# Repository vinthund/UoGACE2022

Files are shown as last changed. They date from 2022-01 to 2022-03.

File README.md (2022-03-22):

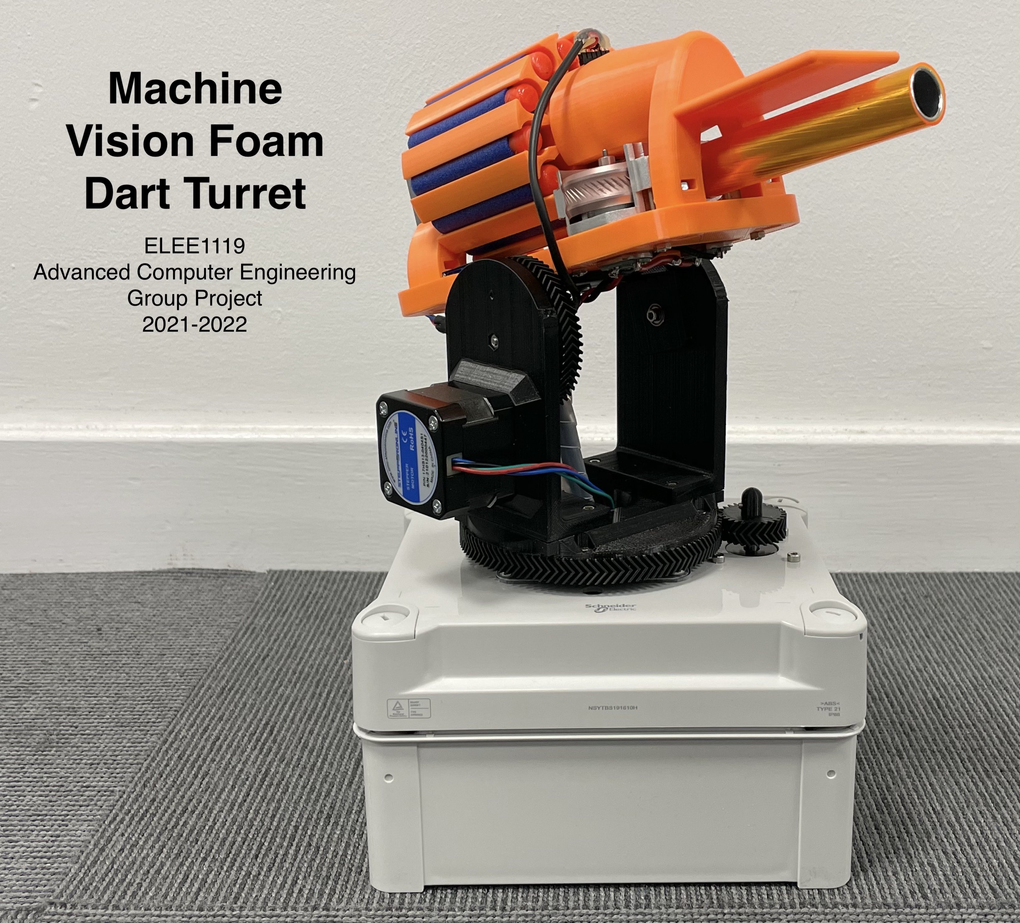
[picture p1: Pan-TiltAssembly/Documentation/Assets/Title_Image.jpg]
Title Image

<br>
## **About the Project**

This project has been developed by the contributors below as a submission of coursework for the University of Greenwich Advanced Computer Engineering Module, academic year 2021/22.

The Machine Vision Foam Dart Turret is a fully automated object targetting system designed to identify, target, and shoot (with a foam dart to two) a person not recognised by the machine vision. It features a 12 dart magazine, 2 axis movement, a Jetson Nano controlled vision system, and two interfaces (one for LAN based web control and video feedback, and one for automatic downloading of this GitHub repo).

Mechanical parts of this project are mostly custom using standard industry parts for difficult to manufacture parts such as stepper motors and bearings. The software is written mostly from scratch, using part libraries where sensible, particularily for the arduino interfacing with hardware, and the Jetson managing its machine vision identification.

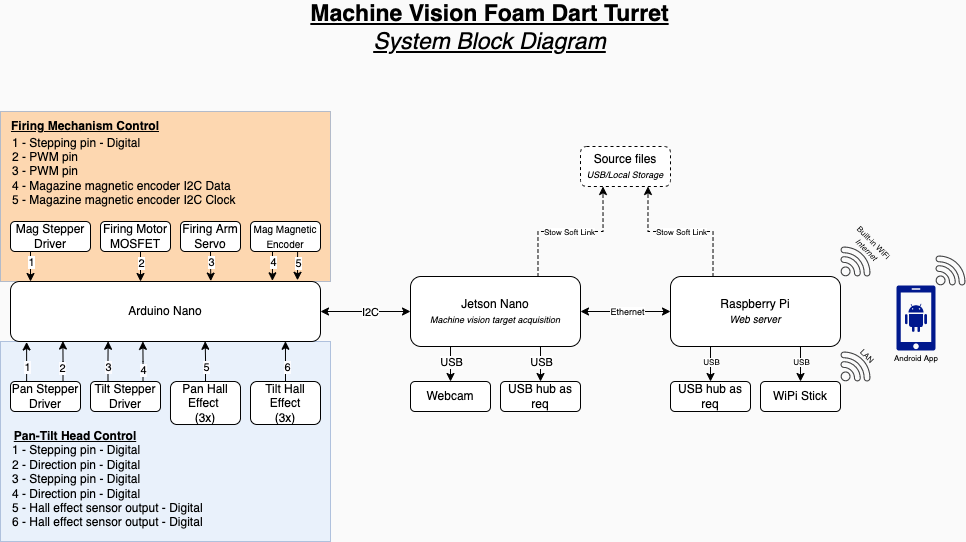
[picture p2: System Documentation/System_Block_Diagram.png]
System block diagram

*System Concept Block Diagram*

## **Contributors**

- [Andrew Dean - ad4646d](https://www.github.com/ad4646d)
- [Chris Halsall - ch6941r -](https://www.github.com/ch6941r)  [AfterEarthLtd](https://www.github.com/AfterEarthLTD)
- [vinthund](https://www.github.com/vinthund)
- [ht5640k - Harshitha Thimmegowda](https://www.github.com/ht5640k)
- [JoelSmalls - Joel A. Okanta](https://www.github.com/JoelSmalls)
- [kamyar123](https://www.github.com/kamyar123)
- [rowBoat](https://www.github.com/rowboat)
<br>

 ## **Viva Video**

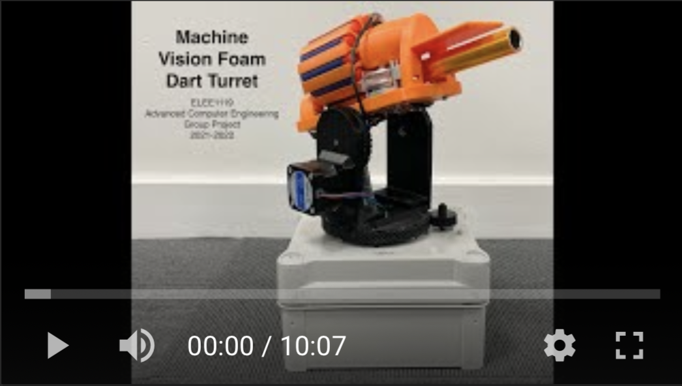
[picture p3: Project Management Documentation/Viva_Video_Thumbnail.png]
Viva_Video_Thumbnail (https://youtu.be/HJBah1AWvD8)


 ## **Firing Mechanism Mechanical Design** - [Chris Halsall - ch6941r](https://www.github.com/ch6941r)

The firing mechanism contains a few pre-made parts including a small stepper motor, the firing motors and barrel, a servo, and a bearing. All other parts have been designed in Fusion 360 and printed in orange PLA on an Ender 3 FDM 3D printer. It features a 12 dart rotary magazine driven by the stepper motor from one end and supported by a bearing at the other end. Through the bearing is mounted a magnet and a magnetic position sensor so that the control electronics can measure the angle of the magazine. A servo is mounted in the base and, with a custom arm, is capable of pushing a dart from the magazine into the firing motors and thus propelling it out of the barrel. A mounting plate is attached to the front of the design to securely mount the camera for machine vision. Finally, a hole and hex slot has been designed in to allow for easy mounting to the pan/tilt mehcanism.

The control electoronics includes an A4988 stepper driver, current limited to 0.5A per phase, an I2C connection for the magnetic position sensor, and a MOSFET (and protection circuitry) for driving the firing motors. These all interface with the joint Arduino Nano that controls all aspects of the moveable mech.
<br>
<br>

## **Pan-Tilt Mechanism Mechanical Design** - [Andrew Dean - ad4646d](https://www.github.com/ad4646d)

The [pan-tilt mechanism](https://github.com/vinthund/UoGACE2022/tree/main/Pan-TiltAssembly) is a bespoke 3D printed mechanism that was designed in tandem with bespoke the [firing mechanism](https://github.com/vinthund/UoGACE2022/tree/ad4646d/3D%20Designs/Firing%20Mech) using AutoDesk Fusion 360.

Herringbone gears were chosen for both pan and tilt axes for a number of reasons:
* They feature minimal backlash compared to 3D printed spur gears
* They are quieter in operation compared to 3D printed spur gears
* More torque can be transmitted through them vs 3D printed spur gears 

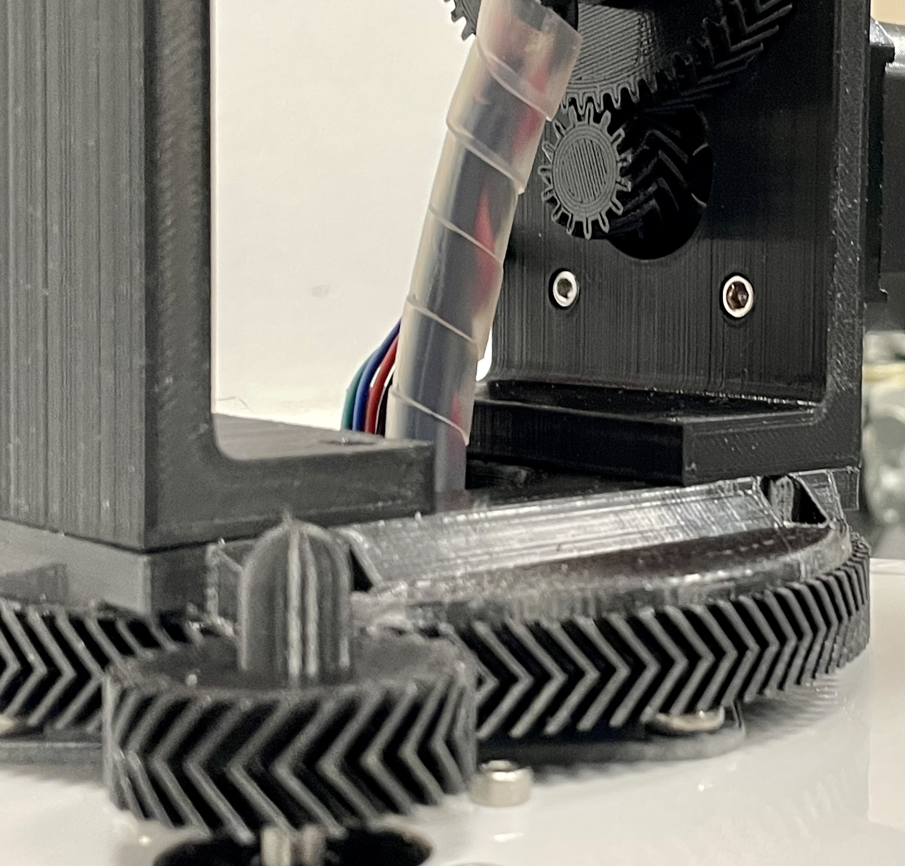
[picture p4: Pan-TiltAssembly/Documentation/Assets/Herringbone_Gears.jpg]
Herringbone_Gears


A plug-in for Fusion 360 called [GF Gear Generator](https://apps.autodesk.com/FUSION/en/Detail/Index?id=1236778940008086660&appLang=en&os=Win64) was used to generate the herringbone gears. \

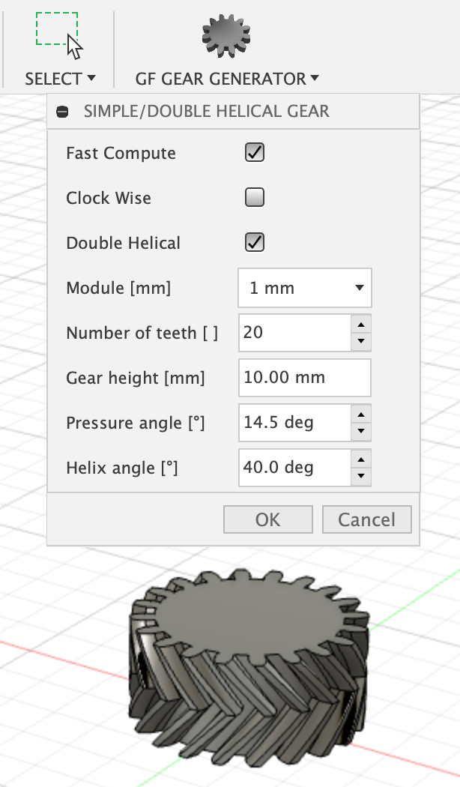
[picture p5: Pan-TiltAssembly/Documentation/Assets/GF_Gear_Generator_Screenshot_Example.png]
GF_Gear_Screenshot
 \
This produces a finished gear as a body, which can then be adapted 

The following parameters were found to produce gears with teeth that printed well and engaged with each other nicely.
> * Module - 1mm
> * Pressure angle - 14.5˚
> * Helix angle - 40˚ 

The number of teeth can be varied but the other parameters must remain the same for all meshing gears; the number of teeth and the module define the diameter of the gear:
> Diameter of gear = module x number of teeth

A gearing ratio of 4:1 was chosen to increase the torque output of the NEMA17 steppers and to give greater step-angle resolution.

The centre distance between the pinion gear and the output gear is calculated as follows:
> Centre distance = (Module*(No. teeth on pinion + No. teeth on output gear))/2

[Flange bearings](https://www.amazon.co.uk/gp/product/B07SHSLTKD/ref=ppx_yo_dt_b_asin_title_o03_s00?ie=UTF8&psc=1) are used to attach the tilt axis to the assembly, highlighted in the cross-section below.
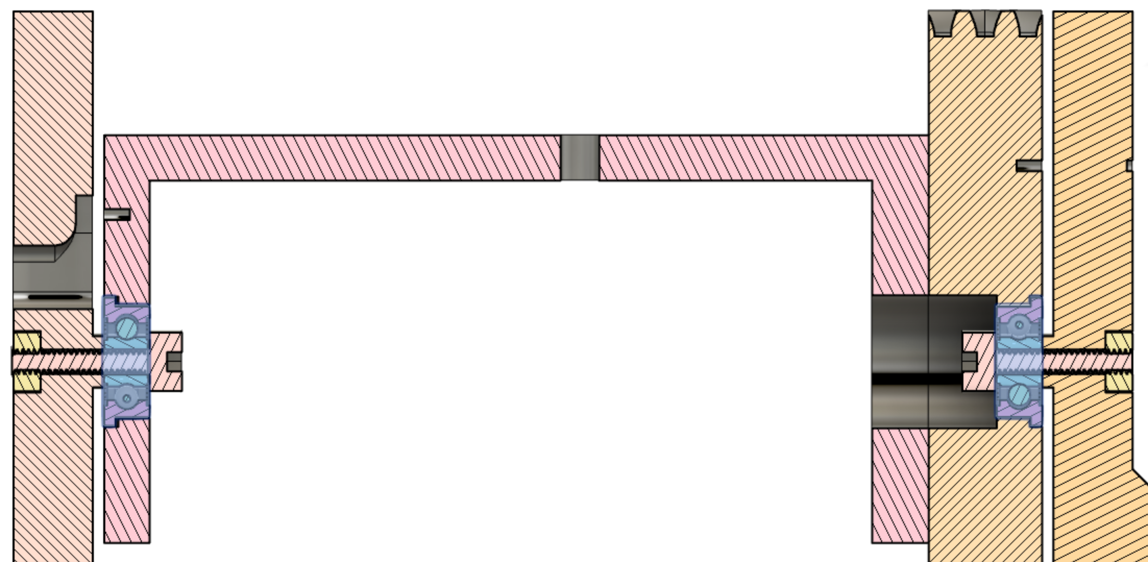
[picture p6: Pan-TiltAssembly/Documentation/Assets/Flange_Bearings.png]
Flange_Bearings
 
These flange bearings interference fit into the firing mech support bracket (pink) and tilt axis gear (yellow), removing the need for glue and simplifying assembly.

Locator pins have been designed into the bases of the two supporting supporting, these help to ensure that both supporting brackets are installed square to eachother, these are highlighted in the image below.
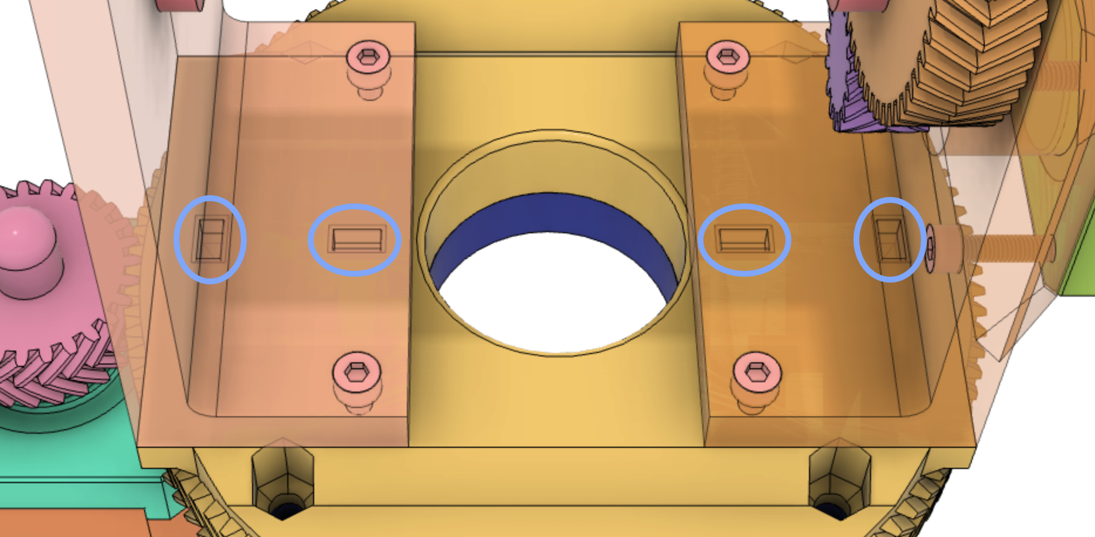
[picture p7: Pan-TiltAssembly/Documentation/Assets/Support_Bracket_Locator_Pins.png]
Locator_pins


All bespoke 3D printed parts for the pan-tilt mechanism were printed in black PLA using an Anycubic i3 Mega.

An [off-the-shelf electronics enclosure](https://www.screwfix.com/p/schneider-electric-ip66-weatherproof-outdoor-enclosure-164-x-105-x-192mm/) was chosen to be the base of the system, this particular enclosure was chosen as it would provide adequate space to house all system components.

A [lazy susan bearing](https://www.stilesandbates.co.uk/75mm-square-lazy-susan-bearing-1709.php) was chosen for the pan axis as it allowed for a convenient way to manage cables between the combined pan-tilt/firing mech and their control electronics in the enclosure below. \
The lazy susan did introduce a lot of audible noise to the system, this is due to a combination of the fact it is an unlubricated bearing and that the enclosure it is attached to was acting like a voice box, amplifying its vibrations. 
A foam pad was added between the bearing and the enclosure and the bearing lubricated with silicone grease, this helped somewhat with the audible noise. Half-step microstepping was also used to reduce the audible noise.

The full parts list for the pan-tilt mechanism can be found [here](https://github.com/vinthund/UoGACE2022/blob/ad4646d/Pan-TiltAssembly/Documentation/Pan-Tilt%20Head%20Parts%20List.pdf).\
STEP files for the pan-tilt mechanism can be found [here](https://github.com/vinthund/UoGACE2022/tree/main/Pan-TiltAssembly/CAD_Files).

<br>

## **Hardware for Pan/Tilt and Firing Mechanisms** - [Chris Halsall - ch6941r](https://www.github.com/ch6941r) & [Andrew Dean - ad4646d](https://www.github.com/ad4646d)
**Pan/Tilt Mechanism Hardware - [Andrew Dean - ad4646d](https://www.github.com/ad4646d)**

NEMA17 stepper motors were chosen for the Pan/Tilt axis as they provided adequate torque output to move both axes, they also feature a step angle of 1.8
* A [NEMA17x34](https://www.omc-stepperonline.com/nema-17-bipolar-1-8deg-26ncm-36-8oz-in-0-4a-12v-42x42x34mm-4-wires.html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) was chosen for the tilt axis
* A [NEMA17x39](https://www.omc-stepperonline.com/nema-17-bipolar-45ncm-6374ozin-15a-42x42x39mm-4-wires-w--1m-pin-connector.html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) was chosen for the pan axis

[A4988 stepper drivers](https://www.amazon.co.uk/gp/product/B07MXXL2KW) were selected for a number of reasons:
* They can drive bi-polar stepper motors up to 2A/phase
* They only require two control pins from the microcontroller to control steps and direction
* They can support microstepping
* They are still readily available amidst the current global component shortage

A combination of [small neodymium magnets](https://www.first4magnets.com/circular-disc-rod-c34/2mm-dia-x-2mm-thick-n42sh-neodymium-magnet-0-15kg-pull-p3327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|ps_1_16690) and [hall effect sensors](https://www.amazon.co.uk/gp/product/B08QCRYXPK) are used to both 'home' each axis and to and to limit the movement on the tilt axis, these were chosen over limit switches as they simplified mechanical assembly and design.

The hardware was connected up on a breadboard for testing ahead of the design of a veroboard prototype control board.

**Firing Mechanism Hardware - [Chris Halsall - ch6941r](https://www.github.com/ch6941r)**

## **Movement Control Circuitry** - [Chris Halsall - ch6941r](https://www.github.com/ch6941r)

A custom circuit board has been designed and built to accomodate the requirements for electrical control. A limitations prevented the use of a custom designed PCB including time, budget, and that continuous development was required therefore dynamically changing the structure of the circuit. A stripboard was chosen as it is relatively versatile and can accomodate throughhole components with ease. 

The bottom of the board is dedicated to power rails, 0V and 12V from an external PSU, and 5V generated by an L7805 linear regulator with the 12V input. All other board components are spread evenly to attempt to seperate wiring connectors as much as possible. The component parts are 
* Arduino Nano
* 3x A4988 stepper motor drivers
* 6x Hall effect sensor headers
* 1x Servo header
* 1x I2C header
* 1x MOSFET, flyback diode, and associated motor header

Some additional capacitors and a diode help to reduce input shock current (and therefore prevent brownout) and reverse power connection damage.

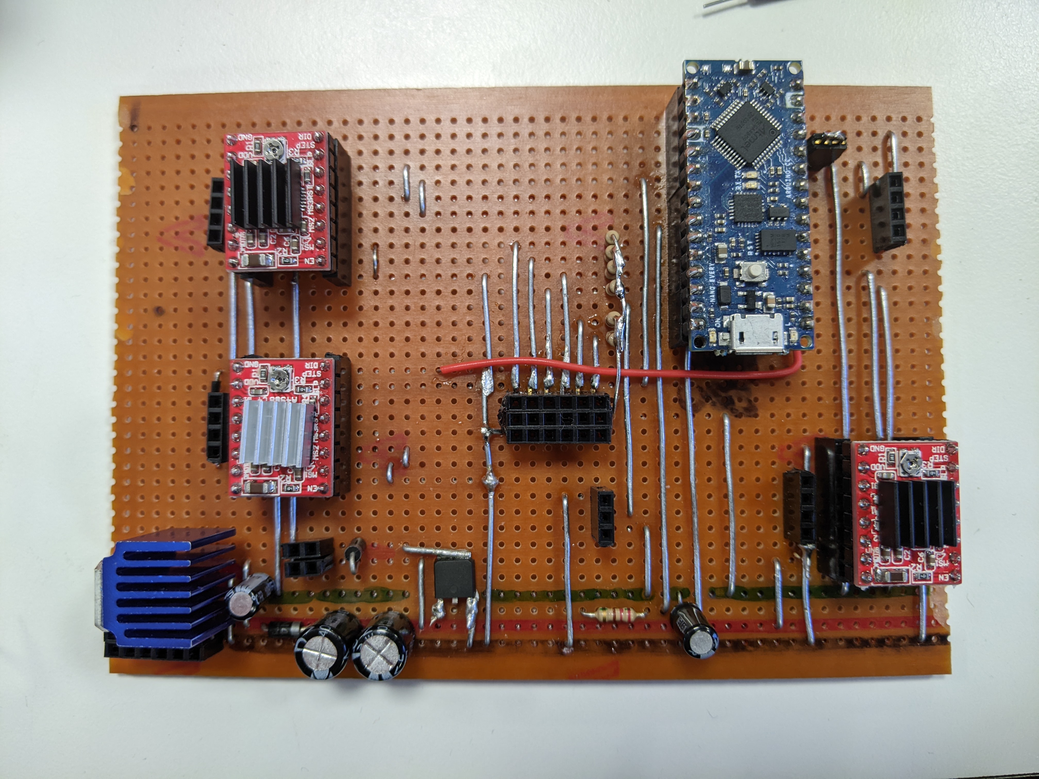
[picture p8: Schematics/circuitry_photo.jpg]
Control Circuitry


<br>

## **Firing Mechanism Communications** - [JoelSmalls - Joel A. Okanta](https://www.github.com/JoelSmalls)

**Items that were used**
* Raspberry Pi 3 Model B+
* Arduino Nano 
* Four Male to Female Jumper wires
* Four Male to Male Jumper wires
* Logic Level Shifter: Bi-Directional Module (Between 3V3 and 5V)
* Ethernet Cable: To allow for ssh into Pi to script in Python.

In order to make the control of the Firing Mechanism possible through communication between the Jetson Nano and the Arduino (shown on above diagram), a communications protocol had to be utilised. Types of communications protocols, such as I2C(Inter-Integrated Circuit), USB(Universal Serial Bus) Serial and SPI(Serial Peripheral Interface) were each investigated to see which would work efficiently when communicating between a Jetson Nano and an Arduino. As a Jetson Nano was not in possession, a Raspberry Pi was instead used to just simulate how certain communications protocols would work with each other.

The first iteration of a communications code between the Arduino and the Raspberry Pi was through USB Serial, in which a USB Cable was required to connect the Arduino straight to the Raspberry Pi. This was a simple type of communication which only required an Arduino USB Cable (dependent on board type) which could freely be moved around due to the length of the cable. However, we  had later anticipated that it would be necessary for a keyboard and mouse USB input to be left available on the Jetson Nano in case of errors. Thus, this idea was scrapped and was moved on to other types of communications protocols.

Other protocols such as I2C and SPI were explored. According to research, when comparing between I2C and SPI, SPI was a faster option; this did not mean it could be instantly utilised though, as not enough examples of communication between an Arduino and a Jetson/Pi could be found online to make use of SPI. Furthermore, it required more wires to be connected to the Nano through a logic level shifter. Due to this, I2C was settled with. 

This, was initially the case, on utilising I2C Communication to transmit data between the Raspberry Pi and the Arduino. Unfortunately though, as the gun firing mech used a sensor which required the Arduino to be a master over I2C, this idea of using I2C could not be applied. Providentially, there was another type of communications I had found through research, named Serial UART. Serial UART, according to research, is a "hardware communication protocol" that uses "asynchronous serial communication", meaning that unlike I2C, it does not have to synchronise to a clock signal. UART was made possible with a library named **SoftwareSerial** on the Arduino, and a library named **Serial** on Python were used to replace the original I2C system implemented.

**Setup**

[I2C]
The Arduino's SDA (Serial Data) was connected to the High Voltage(HV) pin 1, SCL (Serial Clock) at HV2, Arduino 5V at the HV input pin and Arduino Ground to the shifter's Ground. These were connected to the High Voltage due to the Arduino operating at an output of 5V.

The Raspberry Pi's SDA was connected on Low Voltage pin 1, opposite that of the Arduino's SDA connection; SCL was connected to LV2, 3V3 at LV input and Pi Ground to the shifter's ground. The Pi was connected to the Low Voltage side due to the Pi's output voltage being 3V3.

To fully use I2C, the Arduino and the Raspberry Pi's Python 3's libraries were used, being ***wire*** and ***smbus2*** libraries respectively.

[UART]
SoftwareSerial's library allows for the creation of Rx Tx pins over any digital pins, so 2 and 3 were selected in this case. Pin 2, Rx, was connected to HV1 of the logic level shifter; Pin 3 Tx was connected to HV2. Arduino 5V was connected to the HV of the Level Shifter, along with Arduino Ground connected to the component's ground. Similar steps were taken on the opposite side, with the Raspberry Pi's Tx on pin 8 connected on the opposite of the Arduino's Rx. Same followed for the Pi's pin 10 Rx connected opposite the Arduino's Tx on the shifter. The Pi's 3V3 Power was connected to LV, along with the Pi's ground connected to the component's ground.

I22ImagePiArduino

UARTExample

<br>

##  I2C Communicatons , Jetson Nano  - [ht5640k- Harshitha Thimmegowda ](https://www.github.com/ht5640k)

 **Jetson NANO** 

Items used

* Jetson nano
* HDMI cable

To get the Jetson Nano started:
* Basic files were installed.
* Stow was used which is a symlink farm manager which takes distinct sets of software and/or data located in separate directories on the filesystem, and makes them all appear to be installed in a single directory tree.
* Aliases were created to make abrieviation to soomthen the further procedures.
* Created /etc/network/interfaces  

**I2C communications**

Items used

* Raspberry Pi 3 Model B+
* Arduino Nano 
* Four Male to Female Jumper wires
* Four Male to Male Jumper wires
* Logic Level Shifter: Bi-Directional Module (Between 3V3 and 5V)
* Ethernet Cable: To allow for ssh into Pi to script in Python.

Above mentioned items were used to setup a to make an effictive communication to get the hardware working The Arduino's SDA (Serial Data) was connected to the High Voltage(HV) pin 1, SCL (Serial Clock) at HV2, Arduino 5V at the HV input pin and Arduino Ground to the shifter's Ground. These were connected to the High Voltage due to the Arduino operating at an output of 5V.
The Raspberry Pi's SDA was connected on Low Voltage pin 1, opposite that of the Arduino's SDA connection; SCL was connected to LV2, 3V3 at LV input and Pi Ground to the shifter's ground. The Pi was connected to the Low Voltage side due to the Pi's output voltage being 3V3 to get the RapberryPi and Arduino communicating.


**Shortening of ethernet cable**

Items used

* Ethernet cable
* Crimping tool
* Cable Connectors

Above mentioned items were used to shorten a ethernet cable to connect RaspberryPi and Jetson nano, It was done by cutting the available ethernet cable to the required length using a crimping tool and then pushing the wires into the cable connecter. Shortening was required in order to meet the hardware modeling requirement and to adjust the length of the ethernet cable connection very small and convenient.
Screenshot_20220318-221013_Snapchat

<br>

## **Machine Vision Target Aquisition** - [vinthund](https://www.github.com/vinthund)

Motion Detection in Python Version 1.0.0 
Written By Sian Pugh, sp3045k@gre.ac.uk, fleetfootgreyhound@gmail.com, vinthund @ github

Simple backend motion detector written in Python. Intended for use on a Jetson Nano 2gb to communicate with an Arduino system.

Part of a larger project used to control an autonomous nerf sentry - https://github.com/vinthund/UoGACE2022

Currently uses a subtractive method; it will take the first frame of input and store it as the "background", then compare all following frames to this. It has a threshold mechanism in place to ensure that small differences such as shadows are not seen as motion. When motion is detected using this subtractive method, a countour of the motion is drawn, as well as a retangle constructed of the area around it. This rectangle is used for specific targetting; the center is found and then compared to the center of the screen, with the results being sent to the arduino control unit using i2c.

Dependencies: This program requires the numpy and opencv packages to be installed to function. https://numpy.org/ https://opencv.org/

<br>

## **Web Server and Website** - [rowBoat](https://www.github.com/rowboat)

The website consist:
Was constructed using the php files in order to connection and retrieve data from the mysql server.
* The Login page - the first page that the user will see
* The Home page - once the user has logged in this is the next page that they will be greeted by. this page will consist of the window to the view the live video feed from the turret, a reading of how much bullets are left anda button for manual control. 
* A link to the github repository

Webserver
OS: Ubuntu
Wireless or wired: wireless
Configured in a lemp stack using nginx, mysql and php
Created to:
* Host the website
* Store login information
* Store and Retrieve video feed and bullet count from the camera and jetson so it could be displayed on the website and app
* Stores and sends button click to the jetson so when turret reacted to the corresponding button input.

<br>

## **Machine Vision Foam Dart Turret App** - [Kamyar Homampour-kamyar123](https://www.github.com/kamyar123)

This app has few pages which are:

* Login page

* Register page



* Main page

* Live page

Firebase has been used as a database for the login and register page to save all users' information and account date of the last login and created the account.


The main page was supposed to count the bullets, but due to circumstances, it hasn't been completed.

The live page was supposed to show the live stream from the jetson nano camera, but now it shows the test stream for rtsp link to test  if the live stream is actually working.
(https://www.wowza.com/developer/rtsp-stream-test)

<br>

## **Project Management** - [Andrew Dean - ad4646d](https://www.github.com/ad4646d) & [Chris Halsall - ch6941r](https://www.github.com/ch6941r)

When the project was announced, we asked all team members to detail their prior skills and experience on a [shared word document](https://github.com/vinthund/UoGACE2022/blob/main/Project%20Management%20Documentation/ELEE1119%20Team%20List%20(AD%20created).docx).

This initial skillset list was used to inform the project specification and division of tasks, which can be found in [this word document](https://github.com/vinthund/UoGACE2022/blob/main/Project%20Management%20Documentation/Project%20Specification%20and%20Division%20of%20Work%20(rev3).docx).

After everyone had agreed to the contents of the specification and the division of work, a [Gantt chart was created in MS Project](https://github.com/vinthund/UoGACE2022/blob/main/Project%20Management%20Documentation/ELEE1119_Project_Plan_7th_Dec_2021.mpp) to give an overview of the project timeline and to clearly communicate deadlines.

After the Gantt was shared with the team, a [KANBAN was maintained within GitHub](https://github.com/vinthund/UoGACE2022/projects/1). This KANBAN would get updated every Tuesday during the weekly standup meeting to establish what tasks people had in-progress and what tasks they had outstanding.

<br>

## **GitHub Management** - [vinthund](https://www.github.com/vinthund)

***Add your summary of work here and delete this comment.***

<br>

# **License**

Due to the sensitive nature of projectile firing technology, much thought has gone into the ethics of releasing a publically available repository with details of how the project was created. Please note that the content contained within this repository should be used solely for EDUCATION purposes. For full details please see the [License](LICENSE) document found in the root of this repository. This license has been based upon the MIT license.

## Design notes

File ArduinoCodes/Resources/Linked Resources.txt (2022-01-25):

AS5600 Magnetic Position Sensor Library
https://github.com/kanestoboi/AS5600

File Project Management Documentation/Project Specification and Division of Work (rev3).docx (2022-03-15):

# Project Specification and Division of Work

ELEE1119 Advance Computer Engineering

## Project Title

Automatic ‘Nerf’ Sentry Gun utilising Face or Object Recognition and Target Tracking

## Project Brief

To develop a prototype automatic foam dart blaster sentry gun capable of identifying targets, then actively targeting, and firing at them.

## Project Objectives

1. Design and create a custom firing mechanism capable of firing foam “Nerf” darts.
2. Design and create a dynamic mounting system capable of accurately controlling the firing direction.
3. Develop a bullet counting system with scope to incorporate reloading mechanics if the design permits.
4. Develop face or object recognition software capable of identifying predefined threats and feeding back data on their location for targeting.
5. Develop a remotely accessible monitoring and/or control system, e.g. mobile app or hosted website.
6. Develop an automatic log to capture all important activities, e.g. motion detection, user logon, firing at a target, etc.

## Project Methodology

From the ‘Team List’ document our individual skills have been identified.

Team Member’s Skills
Andrew Dean | Chris Halsall | Joshua McField | Kamyar Homampour | Joel Okanta | Sian Leigh Pugh | Harshitha Jayamala Thimmegowda
-Arduino -ESP32 -RasPi -C/C++ -MATLAB -Python -3D Design -Electronics Design | -C/C++ -HTML -CSS -Arduino -3D Design -Electronics Design | -C#/C++ -MATLAB -Javascript -SQL -HTML -CSS -Java -Arduino -Visual Studio -Photography | -C++ -Java -MATLAB -SQL -Arduino -Android Studio | -C#/C++ -MATLAB -Python -Java -SQL -Arduino -RasPi -Android Studio -Electronics | -Arduino -Python -C++ -MATLAB -PHP -Digital Art -Electrical Repair | -C#/C++ -MATLAB -Java -SQL -HTML -Android Studio -Visual Studio -Arduino -RasPi

With team member skills identified it is now possible to split the project into manageable sections with members assigned to tasks that best suit their strengths.

Task | Subtask / Description | Lead | Support 1 | Support 2
Project Management | Creation of GitHub page, govern main repository pull requests, correct any GitHub related issues | Sian | Chris | -
| Physical project management, management of timescales, ensuring a coherent project direction | Andrew | Chris | Sian
Mechatronics | 3D design and manufacture of motorised mounting system. | Andrew | Chris | -
| 3D design and manufacture of foam dart firing system with mechanical support for the camera and any additional sensors. | Chris | Andrew | -
| Design of prototype hardware for driving combined motorised mounting and foam dart firing systems. | Chris | Andrew | -
Software | Writing of software to control motorised mounting system and communications with target acquisition system. | Harshitha | Andrew | Sian
| Writing software to control firing system and communication with target acquisition system. | Joel | Chris | Sian
| Writing of visual recognition software, defining targets and non-targets. | Sian | Joel | Kamyar
| Writing of remotely accessible monitoring/control software (Android app) | Kamyar | Josh | Sian
| Writing of remotely accessible monitoring/control software (webserver and website) | Josh | Kamyar | Sian
| Writing of Error Codes where appropriate | All S/W
| Writing/contributing to logging file to capture all important activities | All S/W
Miscellaneous | Updating README file | All
| Creating supporting documentation where appropriate explaining aspects of the project | All

## Expected Outcomes

1. Fully functioning ‘Nerf’ sentry gun prototype capable of correctly identifying targets, then aiming and accurately firing at those targets.
2. Functional remotely accessible monitoring system with video feed and sentry position information. Possibility of control including sleep and wake commands, adding and removing persons from the target list, and manual control of the sentry’s position.

## Ethical Considerations

While the aims of the project hold a humorous note, autonomising a foam dart blaster, the technology could easily be adapted to create a considerable threat to life. Therefore, it is important to consider the associated ethics. An appropriate license should be used to limit how the associated code is used. Further considerations shall be covered in the project report.

## Health and Safety

It is important to consider the health and safety of all persons in the immediate vicinity of the project, especially during active testing. The following risk management table has been created to ensure safety is upheld. Likelihood and Severity are measured out of 5 with 5 as the most likely or severe.

Risk | Likelihood | Severity | Mitigation
RSA, eye strain, other office related injuries | 3 | 2 | All members to take regular breaks, ensure equipment is correctly setup (correct screen height, etc).
Eye Injury from foam blaster | 3 | 4 | When blaster is ‘charged’ it is to be put in a position where it is impossible for a foam dart to directly enter the eye OR Members to wear eye protection. Code to be developed to specifically target the center of mass of a person or object.
Electrical Shock | 2 | 5 | Where possible, avoid working with home 230VAC. Instead, prefer consumer power supplies. If working with higher voltages, ensure the supply is isolated while handling components or wiring.
Mechanical Injuries | 2 | 3 | Use correct techniques when handling power or hand tools. Ensure power to moving parts is isolated before handling them. Consciously design out mechanical entrapment risks.

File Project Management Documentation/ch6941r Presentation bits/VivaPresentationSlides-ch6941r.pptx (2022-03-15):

## Mission

- Develop a prototype Foam Dart Blaster Sentry Gun, capable of identifying targets, actively targeting, and accurately firing at them.

Objectives

Design and create a custom firing mechanism capable of firing foam “Nerf” darts.
Design and create a dynamic mounting system capable of accurately controlling the firing direction.
Develop a bullet counting system with scope to incorporate reloading mechanics if the design permits.
Develop face or object recognition software capable of identifying predefined threats and feeding back data on their location for targeting.
Develop a remotely accessible monitoring and/or control system, e.g. mobile app or hosted website.
Develop an automatic log to capture all important activities, e.g. motion detection, user logon, firing at a target, etc.

## System Overview and Division of Work

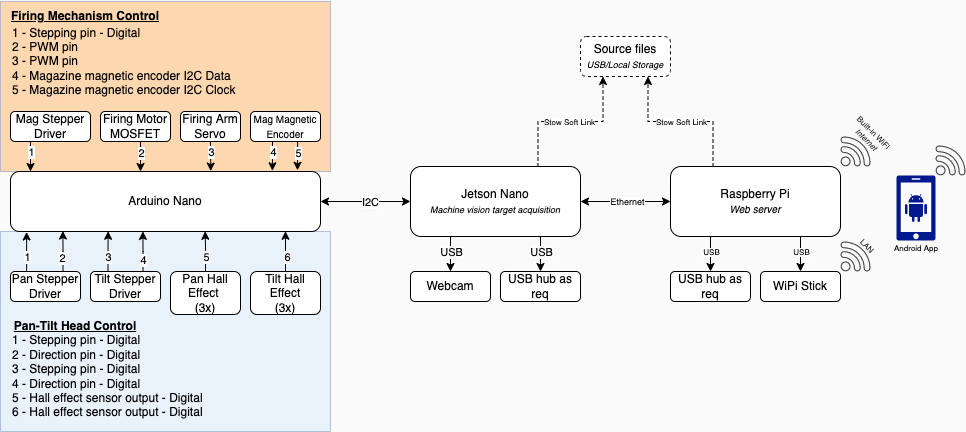
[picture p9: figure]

Mechatronics | | Software | | | | Project
Pan and Tilt Mechanism and Circuitry | Firing Mech and Circuitry | Inter-board Comms | Machine Vision | Webserver | Mobile Application | Project Management
Andrew | Chris | Joel and Harshitha | Sian | Josh | Kamyar | Andrew

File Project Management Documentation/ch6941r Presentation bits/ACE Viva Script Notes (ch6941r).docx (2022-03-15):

# ACE Viva Script Notes - ch6941r

Hello and welcome to this presentation on our Machine Vision Foam Dart Turret.
Our mission for this project, made for Advanced Computer Engineering, was to develop a prototype foam dart blaster sentry gun capable of identifying targets, actively targeting, and accurately firing at them.

Our initial outset objectives were

1. Design and create a custom firing mechanism capable of firing foam “Nerf” darts.
2. Design and create a dynamic mounting system capable of accurately controlling the firing direction.
3. Develop a bullet counting system with scope to incorporate reloading mechanics if the design permits.
4. Develop face or object recognition software capable of identifying predefined threats and feeding back data on their location for targeting.
5. Develop a remotely accessible monitoring and/or control system, e.g. mobile app or hosted website.
6. Develop an automatic log to capture all important activities, e.g. motion detection, user logon, firing at a target, etc. (10sec)

After deciding upon the scope of our project we pooled our strengths and passions, developed this system overview, and split up the workload into the following manageable chunks. Each member also had support from other members if needed, especially where sections overlap or interact. We’re going to move left to right in this table to describe to you, in detail, what each section involves.

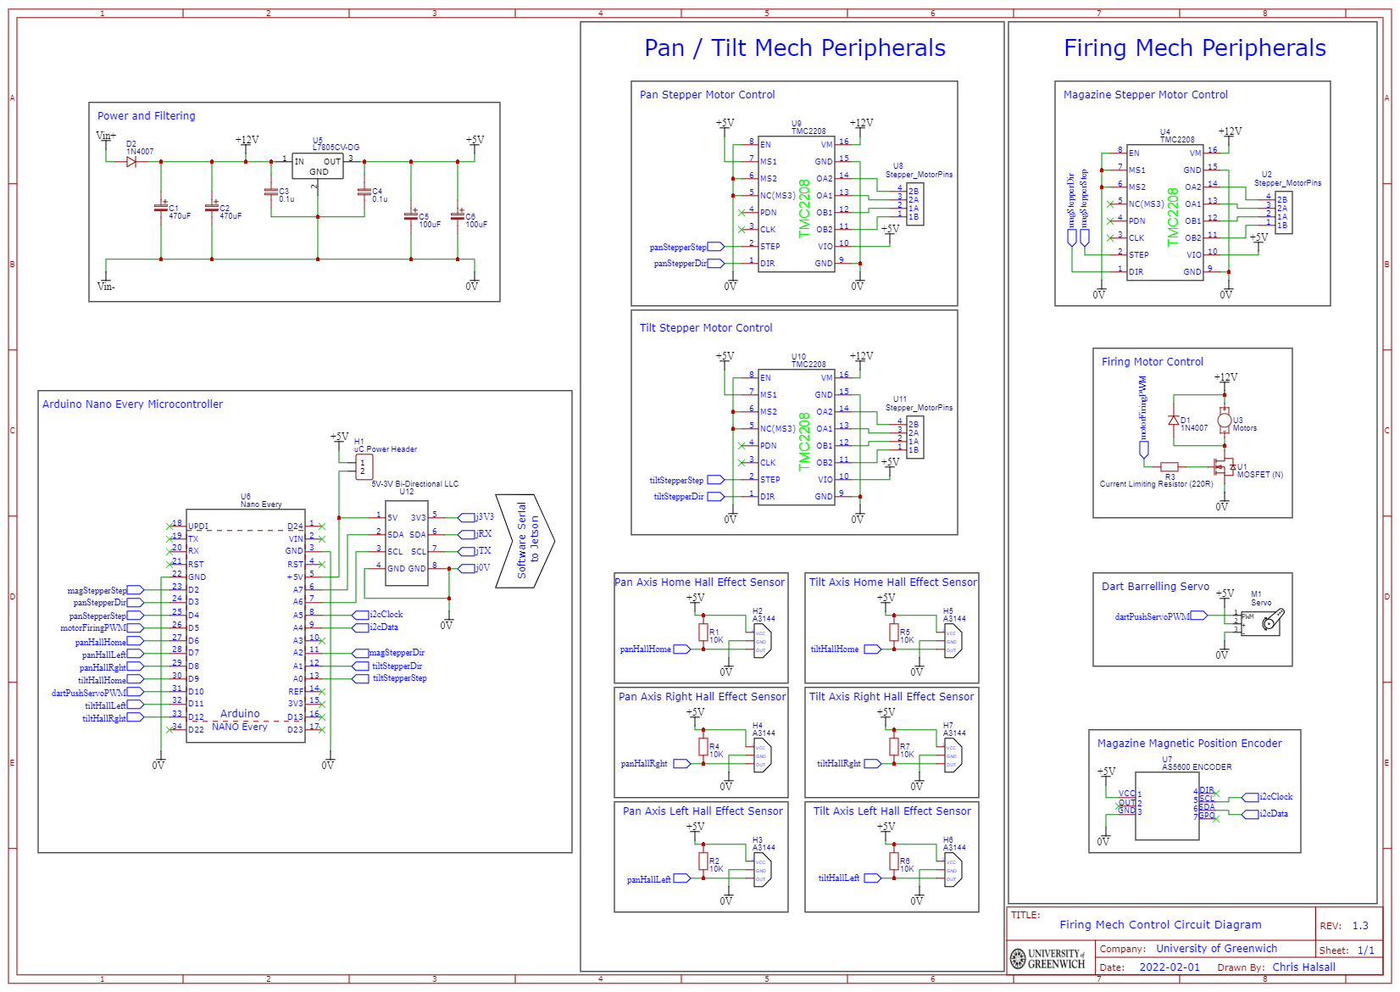
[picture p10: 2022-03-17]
Schematics/Schematic_UoGACE2022 Control Board_2022-03-17.png

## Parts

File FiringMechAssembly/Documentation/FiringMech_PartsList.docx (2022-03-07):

# Firing Mech Parts List

Table 1 - Document History
Revision | Initials | Date | Description
Rev 1 | CH | 23rd Feb 2022 | Document created (Template AD)

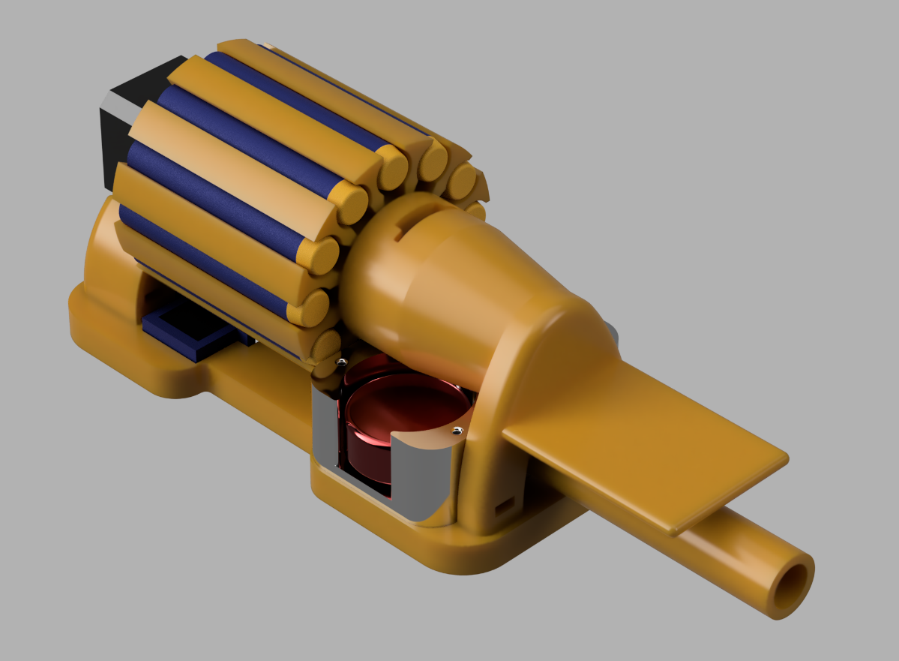
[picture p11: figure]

Figure 1 - Render of Firing Mech Assembly

Table 2 – 3D Printed Parts
Part Number | Image of Part | Description of Part | Quantity | GitHub Link

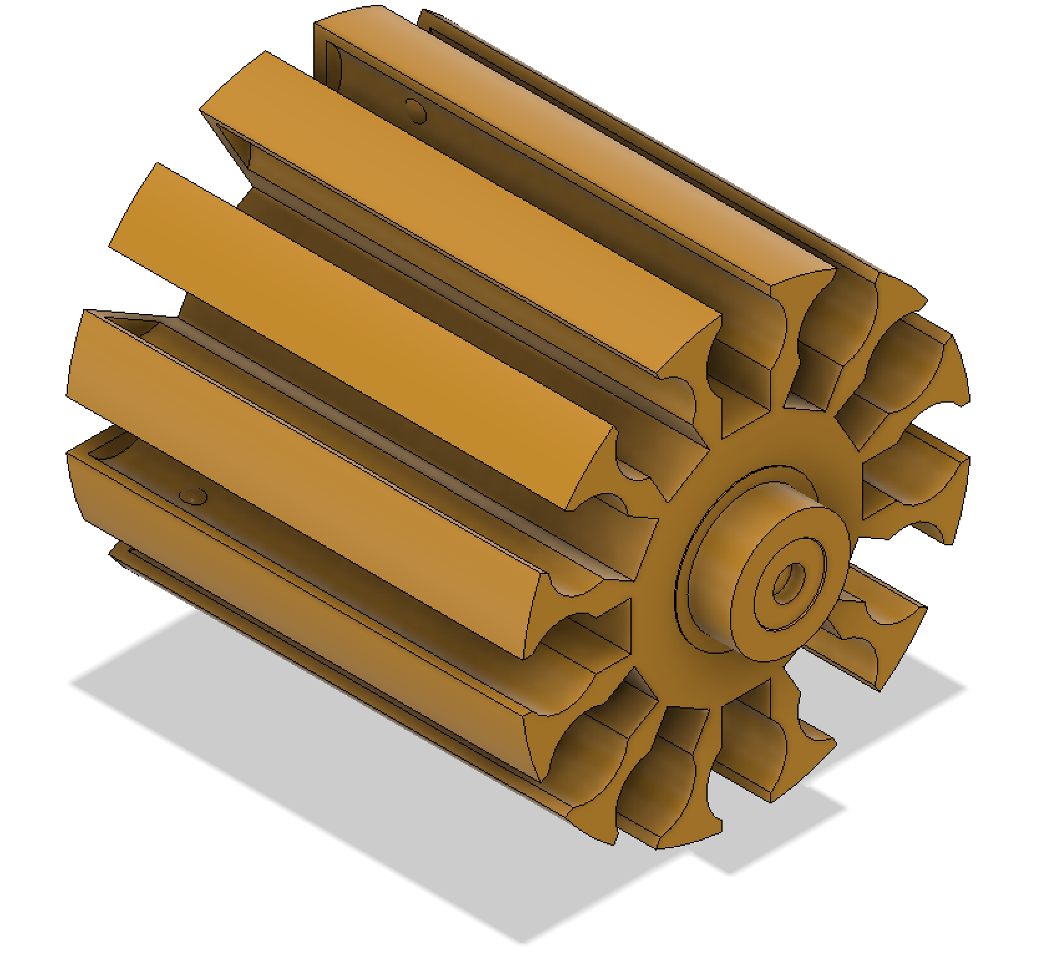
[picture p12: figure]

3DP-9 | | 12 Dart Magazine | 1 | Link Here

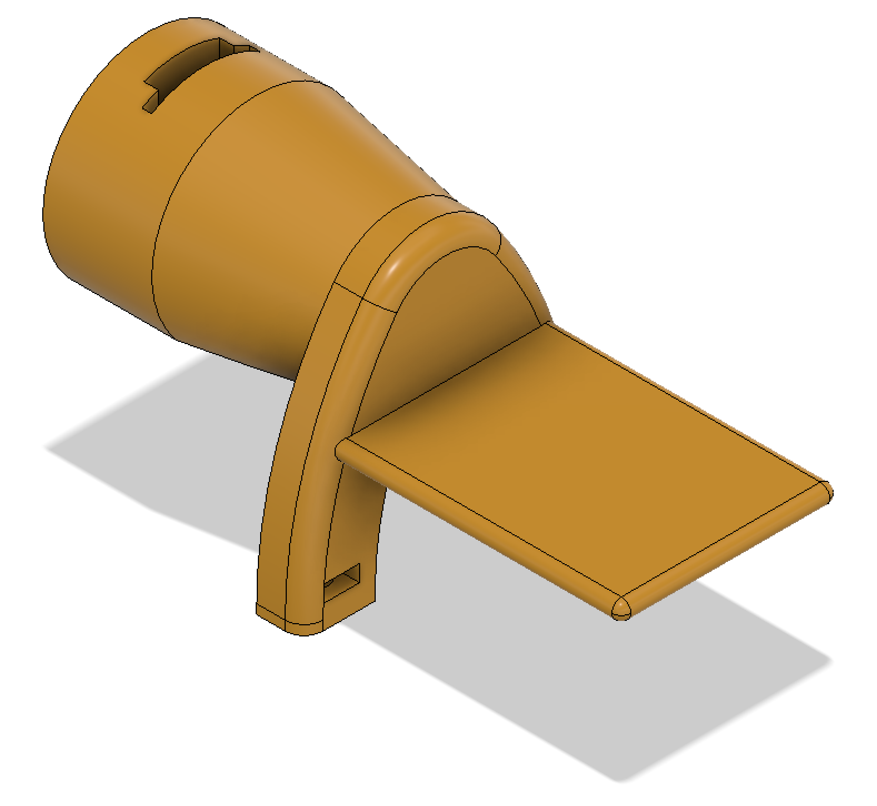
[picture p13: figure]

3DP-10 | | Bearing Holder (Supports camera) | 1 | Link Here

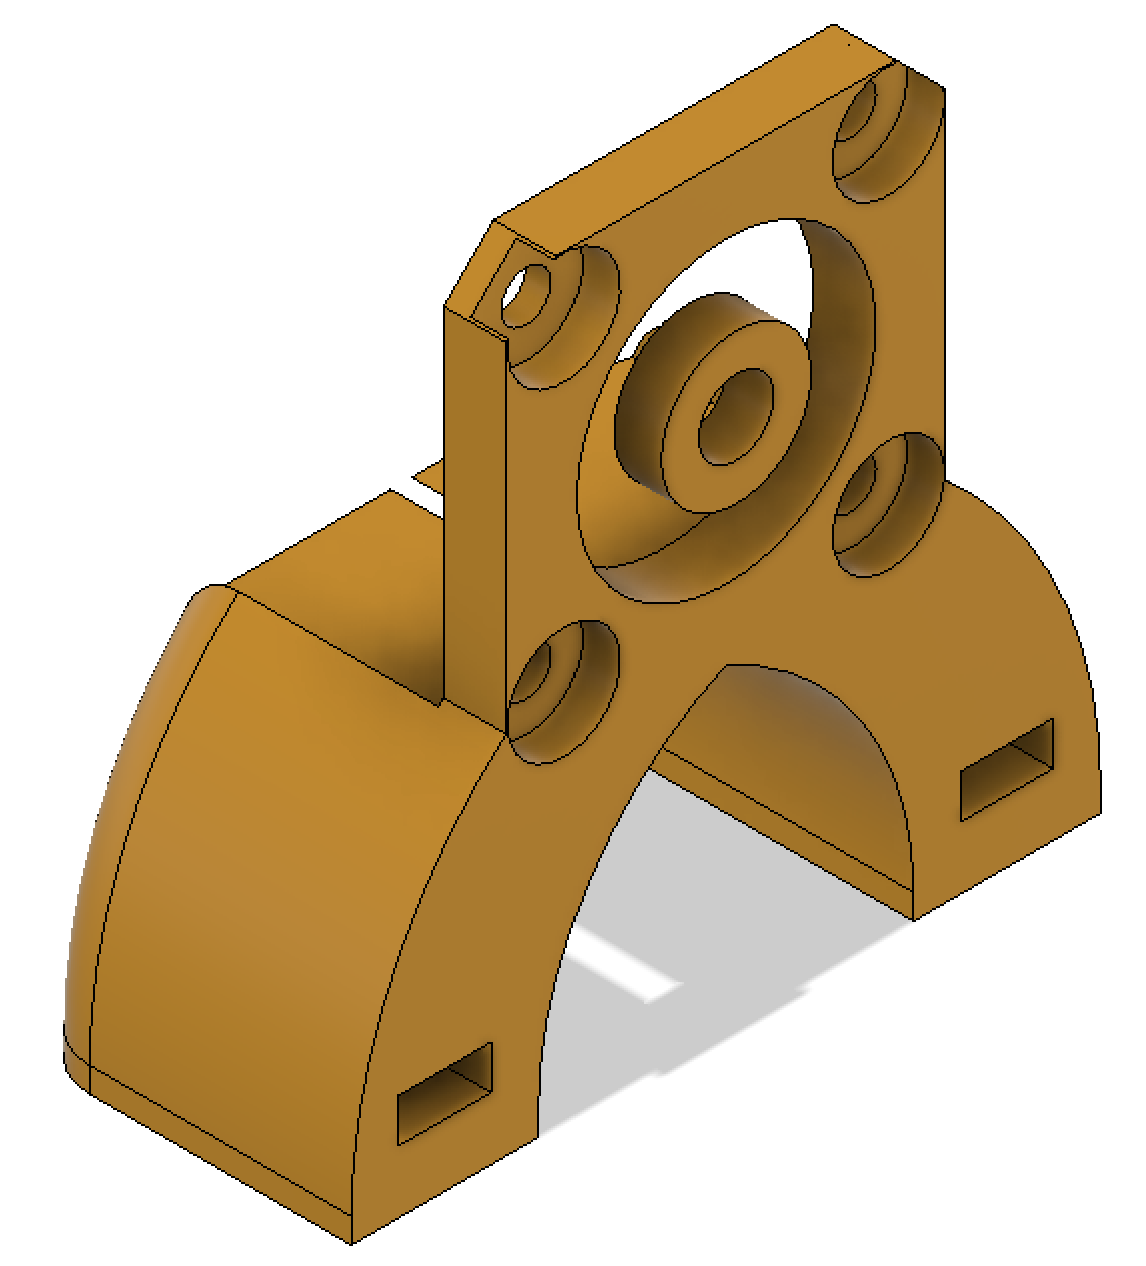
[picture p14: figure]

3DP-11 | | Stepper Holder | 1 | Link Here

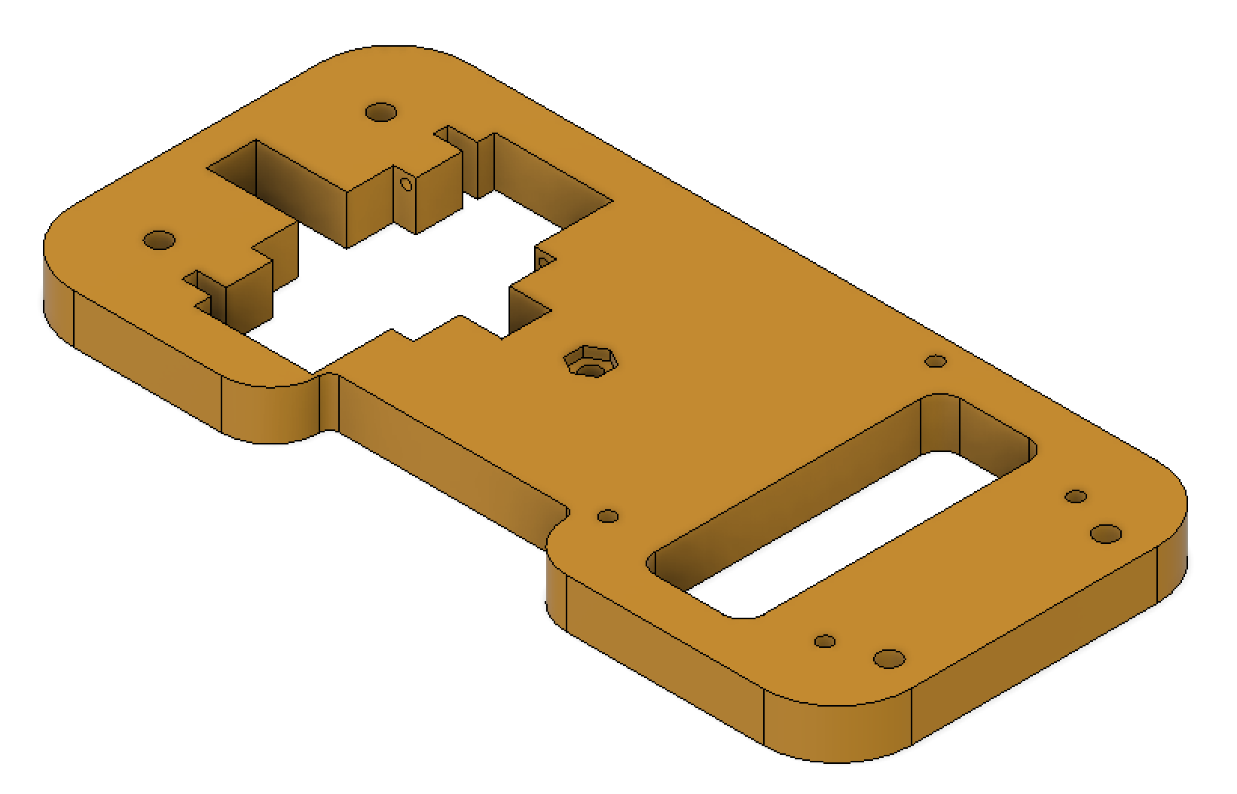
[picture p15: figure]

3DP-12 | | Baseplate | 1 | Link Here

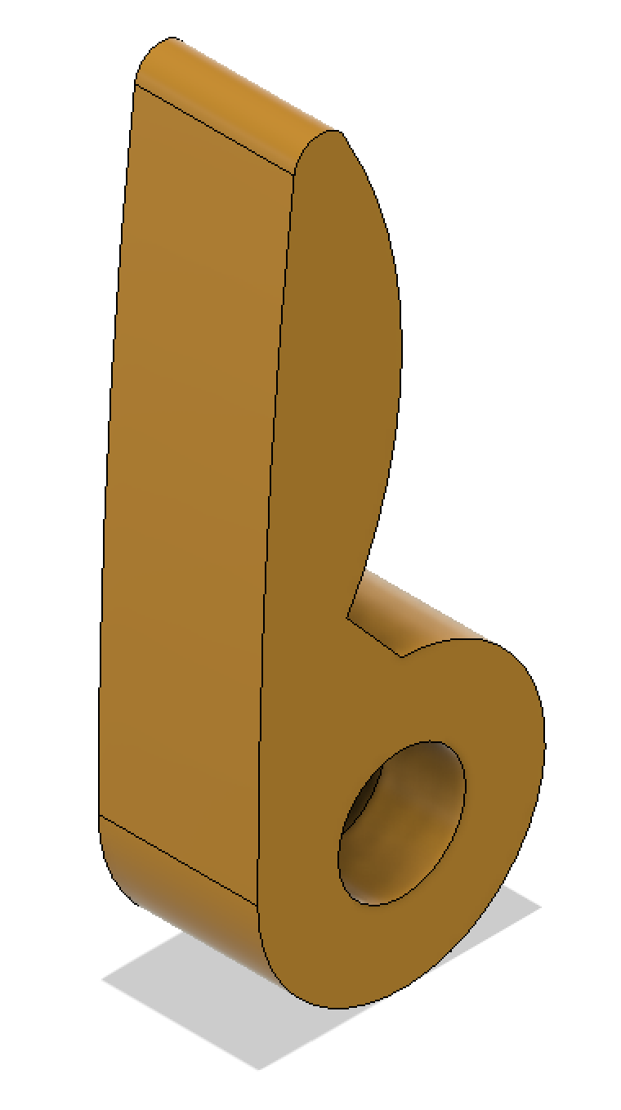
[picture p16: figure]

3DP-13 | | Servo Arm | 1 | Link Here

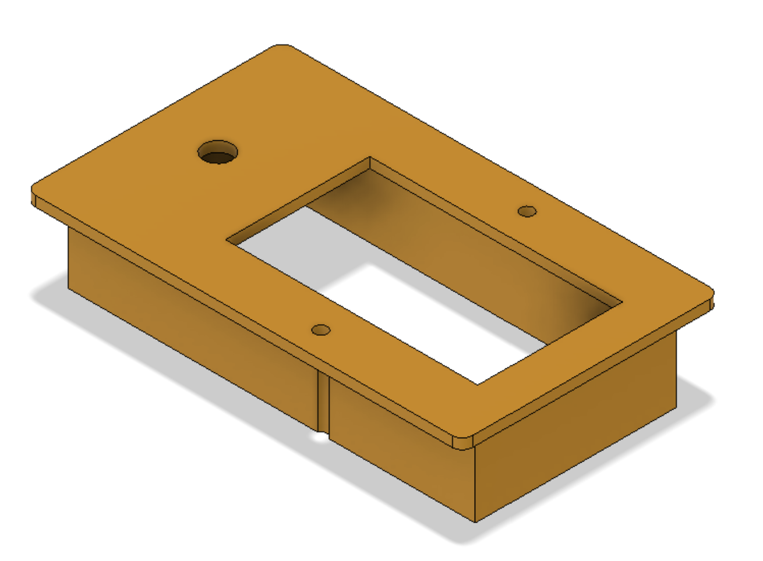
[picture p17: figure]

3DP-14 | | PSU Case Lid | 1 | Link Here

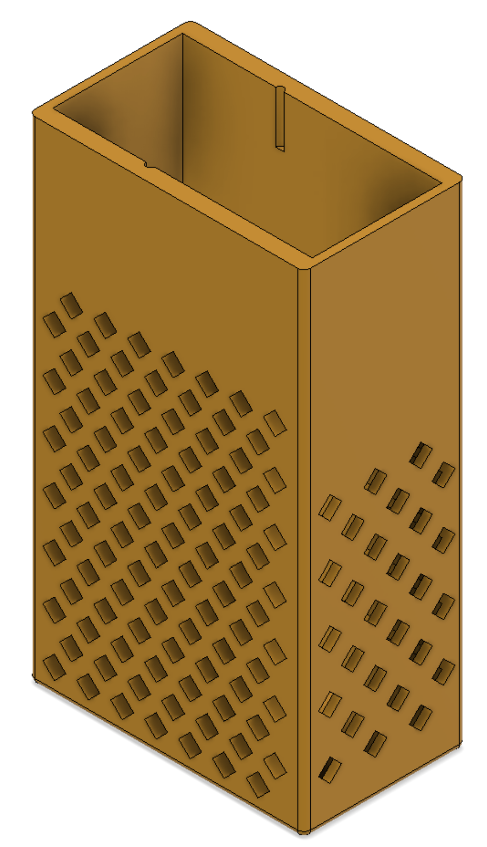
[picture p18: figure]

3DP-15 | | PSU Case Body | 1 | Link Here

Table 3 – Off-The-Shelf Parts
Part Number | Qty | Description | Manufacturer | MFN PN
LAU1 | 1 | Dart Launcher Upgrade Kit | Worker Mod | W0315 (https://www.etsy.com/uk/listing/773251736/worker-mod-flywheel-diagonal-mental-type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)
BR3 | 1 | Plain Race Bearing (20mm ID, 32mm OD) | RS PRO | 6804-2RS (https://uk.rs-online.com/web/p/ball-bearings/6190323/?searchHistory=%7B%22enabled%22%3Atrue%7D)
MTR3 | 1 | NEMA 14 Stepper Motor | Schneider Electric | NEMA14 (https://www.imshome.com/downloads/datasheets/Nema14_motors.pdf)
SEN2 | 1 | AS5600 Magnetic Position Sensor | | AS5600 (https://www.ebay.co.uk/itm/313603433699)
DRIV2 | 1 | TMC2208 Stepper Motor Driver | TMC | TMC2208 (https://www.ebay.co.uk/itm/353868844618?hash=item52643a0e4a:g:5qEAAOSwxjZgLhU9)
9g Servo | 1 | Micro Servo | Lofty Ambition | MG90S (https://www.ebay.co.uk/itm/283464089727)
FX-Various | ~ | Various M4 Fixings including hex nuts and bolts. | - | -

Chris HalsallFiring Mech Parts List - Rev 1ELEE1119 - ACE

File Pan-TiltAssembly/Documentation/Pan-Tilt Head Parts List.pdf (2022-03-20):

Andrew Dean | Pan-Tilt Head Parts List - Rev 4 | ELEE1119 - ACE

# Pan-Tilt Head Parts List

Table 1 - Document History
Revision | Initials | Date | Description
Rev 1 | AWD | 6 th Feb 2022 | Document created
Rev 2 | AWD | 15th Feb ‘22 | Added foam sheet
Rev 3 | AWD | 19 th Feb ‘22 | Added ‘Hall Effect Pan Mount’ Added 3x additional M3 Hexagon Nut – SS Added 3x additional M3x6 Hex Cap Head – SS
Rev 4 | AWD | 19th Mar ‘22 | Removed 2x ‘Hall Effect Pan Mount’ Removed 2x M3 Hexagon Nut – SS (FX1) Removed 2x M3x6 Hex Cap Head – SS (FX9) Removed 2x Hall Effect Sensors (SEN1)


Figure 1 - Render of Pan-Tilt Head Assembly

Part Number; Image of Part; Description of Part; Quantity; GitHub Link; Tilt Gear – 60 teeth; Click here (https://github.com/vinthund/UoGACE2022/blob/main/Pan-TiltAssembly/CAD_Files/Tilt_Gear_60T.step); Tilt Pinion – 15 teeth; Click here (https://github.com/vinthund/UoGACE2022/blob/main/Pan-TiltAssembly/CAD_Files/Tilt_Pinion_15T.step); Pan Gear – 108 teeth; Click here (https://github.com/vinthund/UoGACE2022/blob/main/Pan-TiltAssembly/CAD_Files/Pan_Gear_108T.step); Pan Pinion – 27 teeth; Click here (https://github.com/vinthund/UoGACE2022/blob/main/Pan-TiltAssembly/CAD_Files/Pan_Pinion_27T.step); Firing Mech Bracket; Click here (https://github.com/vinthund/UoGACE2022/blob/main/Pan-TiltAssembly/CAD_Files/Firing_Mech_Bracket_V1.step)

Table 2 – 3D Printed Parts

Table 2 – 3D Printed Parts
Part Number | Image of Part | Description of Part | Quantity | GitHub Link


3DP-6 | | Tilt Gear and Stepper Support | 1 | Click here (https://github.com/vinthund/UoGACE2022/blob/main/Pan-TiltAssembly/CAD_Files/Tilt_Gear_Stepper_Support.step)
3DP-7 | | Firing Mech Bracket Support | 1 | Click here (https://github.com/vinthund/UoGACE2022/blob/main/Pan-TiltAssembly/CAD_Files/Firing_Mech_Bracket_Support.step)
3DP-8 | | Hall Effect Pan Mount | 1 | Click here (https://github.com/vinthund/UoGACE2022/blob/main/Pan-TiltAssembly/CAD_Files/Hall_Effect_Pan_Mount.step)

Table 3 – Off-The-Shelf Parts
Part Number | Qty | Description | Manufacturer | MFN PN
FX1 | 11 | M3 Hexagon Nut – SS | Accu | HPN-M3-A2 (https://www.accu.co.uk/en/hexagon-nuts/7888-HPN-M3-A2)
FX2 | 4 | M4 Hexagon Nut – SS | Accu | HPN-M4-A2 (https://www.accu.co.uk/en/hexagon-nuts/7890-HPN-M4-A2)
FX3 | 4 | M4 Hexagon Nut Nyloc - SS | Accu | HNN-M4-A2 (https://www.accu.co.uk/en/hexagon-nylon-locking-nuts/7946-HNN-M4-A2)
FX4 | 4 | M4x8 Pozi Pan Head - SS | Accu | SPP-M4-8-A2 (https://www.accu.co.uk/en/pozi-pan-head-screws/9295-SPP-M4-8-A2)
FX5 | 4 | M4x6 Pozi Pan Head - SS | Accu | SPP-M4-6-A2 (https://www.accu.co.uk/en/pozi-pan-head-screws/9294-SPP-M4-6-A2)
FX6 | 8 | M3x16 Hex Cap Head - SS | Accu | SSCF-M3-16-A2 (https://www.accu.co.uk/en/cap-head-screws/3822-SSCF-M3-16-A2)
FX7 | 2 | M3x12 Hex Cap Head - SS | Accu | SSCF-M3-12-A2 (https://www.accu.co.uk/en/cap-head-screws/3820-SSCF-M3-12-A2)
FX8 | 4 | M3x8 Hex Cap Head – SS | Accu | SSCF-M3-8-A2 (https://www.accu.co.uk/en/cap-head-screws/3818-SSCF-M3-8-A2)
FX9 | 5 | M3x6 Hex Cap Head – SS | Accu | SSCF-M3-6-A2 (https://www.accu.co.uk/en/cap-head-screws/3817-SSCF-M3-6-A2)
FX10 | 2 | M3x5 Cup Point Grub - SS | Accu | SSU-M3-5-A2 (https://www.accu.co.uk/en/cup-point-set-screws/5010-SSU-M3-5-A2)
BR1 | 2 | 3x10x4mm Flange Bearing | Sourcing Map | F623ZZ (https://www.amazon.co.uk/gp/product/B07SHSLTKD)
BR2 | 1 | 75x75mm Lazy Susan Bearing | Stiles & Bates | LS75S (https://www.stilesandbates.co.uk/75mm-square-lazy-susan-bearing-1709.php)
MTR1 | 1 | NEMA17 42x42x34mm | OMC Stepper Online | 17HS13-0404S1 (https://www.omc-stepperonline.com/nema-17-bipolar-1-8deg-26ncm-36-8oz-in-0-4a-12v-42x42x34mm-4-wires.html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)
MTR2 | 1 | NEMA17 42x42x39mm | OMC Stepper Online | 17HS15-1504S-X1 (https://www.omc-stepperonline.com/nema-17-bipolar-45ncm-6374ozin-15a-42x42x39mm-4-wires-w--1m-pin-connector.html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)
MAG1 | 2 | 2x2mm Neodymium Magnet – 0.15kg Pull - Cylindrical | First4magnets | F412SH-20 (https://www.first4magnets.com/circular-disc-rod-c34/2mm-dia-x-2mm-thick-n42sh-neodymium-magnet-0-15kg-pull-p3327)
SEN1 | 6 | Hall Effect Sensor | Allegro Microsystems | OH3144E (https://www.amazon.co.uk/gp/product/B08QCRYXPK)
DRIV1 | 2 | A4988 Stepper Motor Driver | ARCELI | A4988 (https://www.amazon.co.uk/gp/product/B07MXXL2KW)
MCU1 | 1 | Arduino Nano Every | Arduino | ABX00033 (https://store.arduino.cc/products/arduino-nano-every-with-headers)
BOX1 | 1 | Enclosure 164x105x192mm | Schneider Electric | NSYTBS191610H (https://www.screwfix.com/p/schneider-electric-ip66-weatherproof-outdoor-enclosure-164-x-105-x-192mm/576hv)
FOAM1 | 1 | Grey Foam Sheet 22.5cm x 30cm | Hobbycraft | 6583621003 (https://www.hobbycraft.co.uk/grey-foam-sheet-225cm-x-30cm/658362-1003)

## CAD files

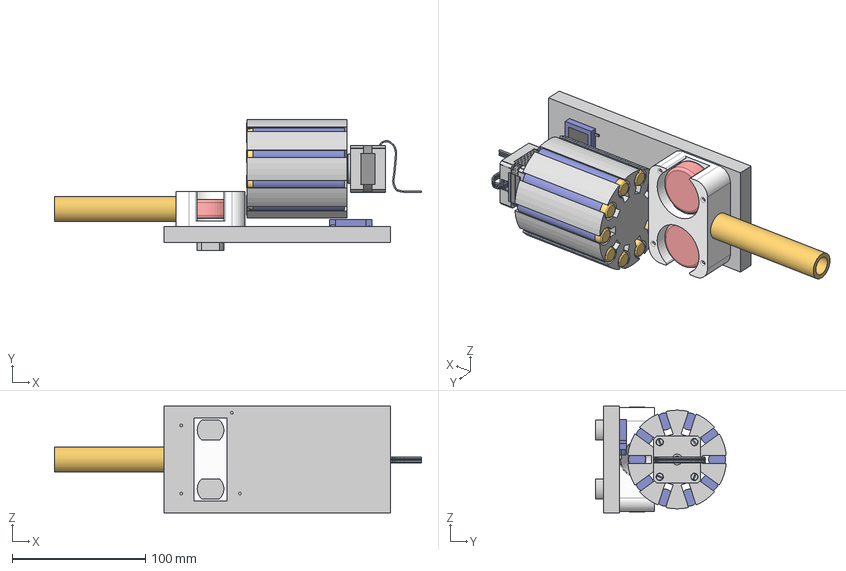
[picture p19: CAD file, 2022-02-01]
FiringMechAssembly/3D Designs/Concept Designs/Firing Mech Concept 1 v6.step
275.1 x 97.9 x 80.0 mm
Nerf Bullet x 10
Launcher
Lagerschild_14
Welle_14
Stator_14
Kollektorschild_14
Schraube_M3x5 x 4
Connector_14
Micro Servo 9g

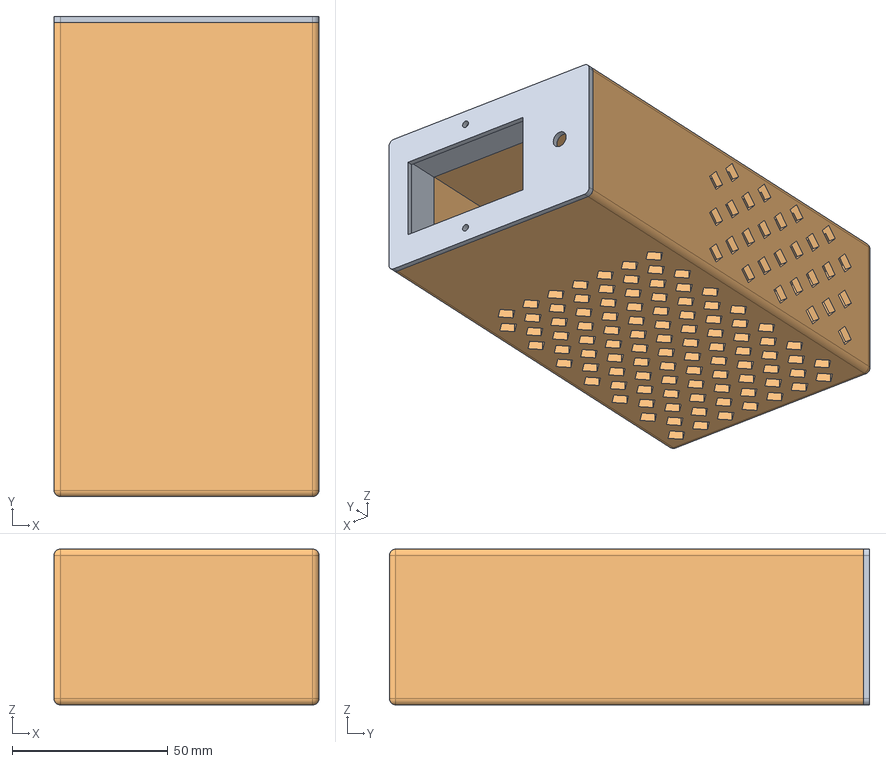
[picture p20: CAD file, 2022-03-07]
FiringMechAssembly/3D Designs/Final Design/PSU Case v1.step
85.0 x 154.0 x 50.0 mm

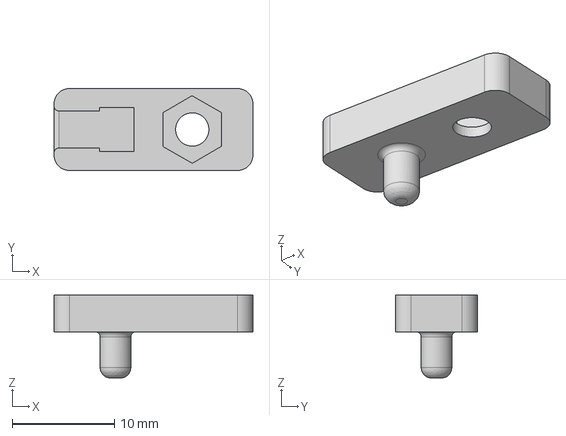
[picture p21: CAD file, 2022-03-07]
Pan-TiltAssembly/CAD_Files/Hall_Effect_Pan_Mount.step
19.4 x 8.00 x 8.10 mm

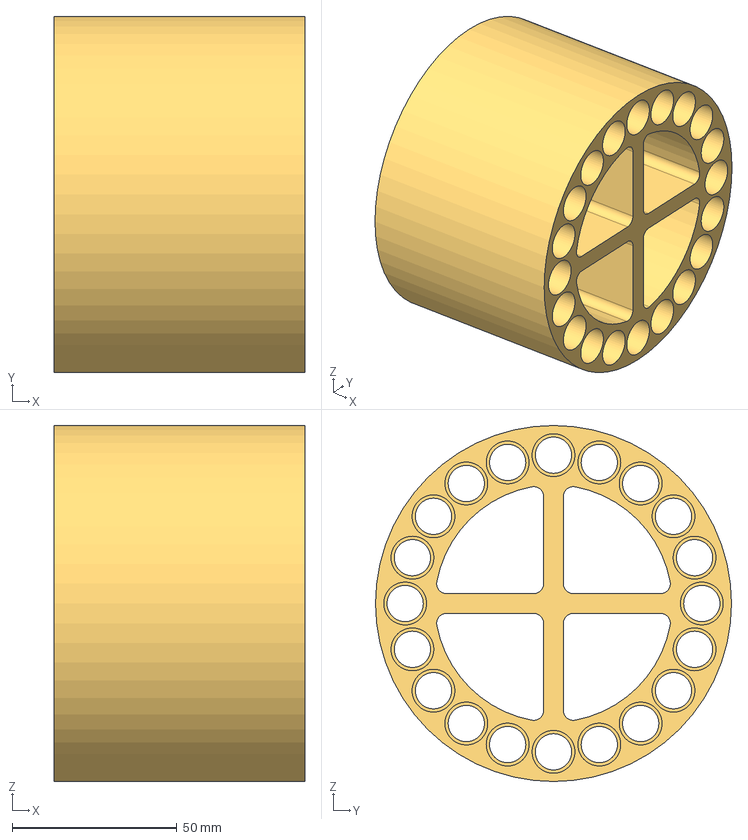
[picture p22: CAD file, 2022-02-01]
FiringMechAssembly/3D Designs/Concept Designs/Circular 20 Dart Magazine Concept v2.step
76.0 x 108.0 x 108.0 mm

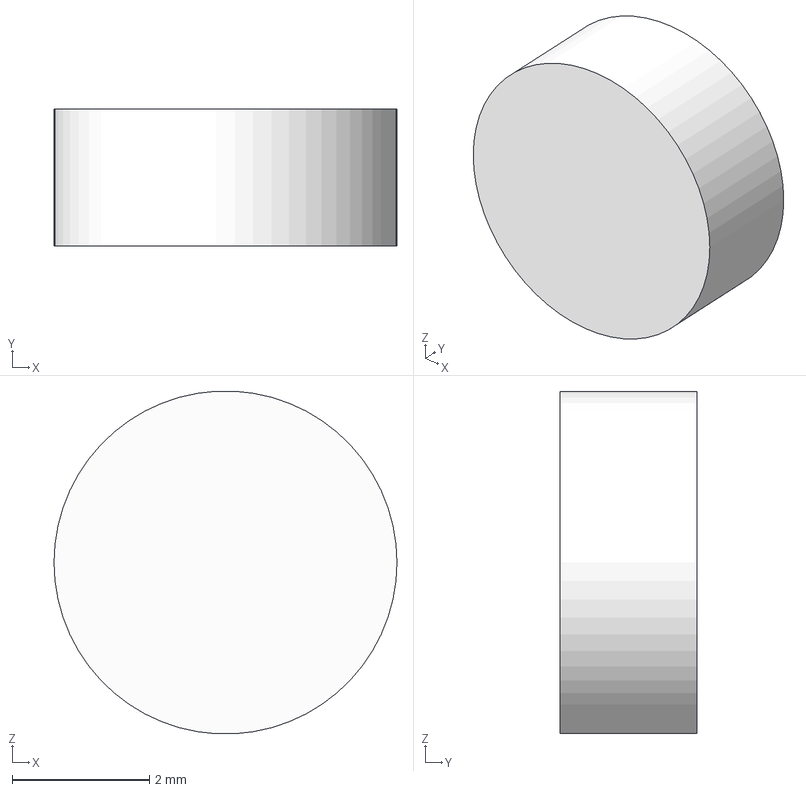
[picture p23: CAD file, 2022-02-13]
FiringMechAssembly/3D Designs/Final Design/Magnet v2.step
5.00 x 2.00 x 4.99 mm

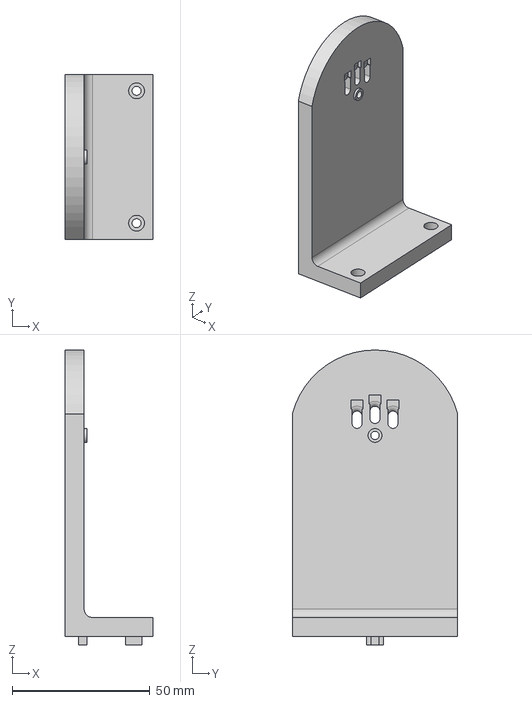
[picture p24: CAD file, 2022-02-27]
Pan-TiltAssembly/CAD_Files/Firing_Mech_Bracket_Support.step
32.0 x 60.0 x 107.0 mm

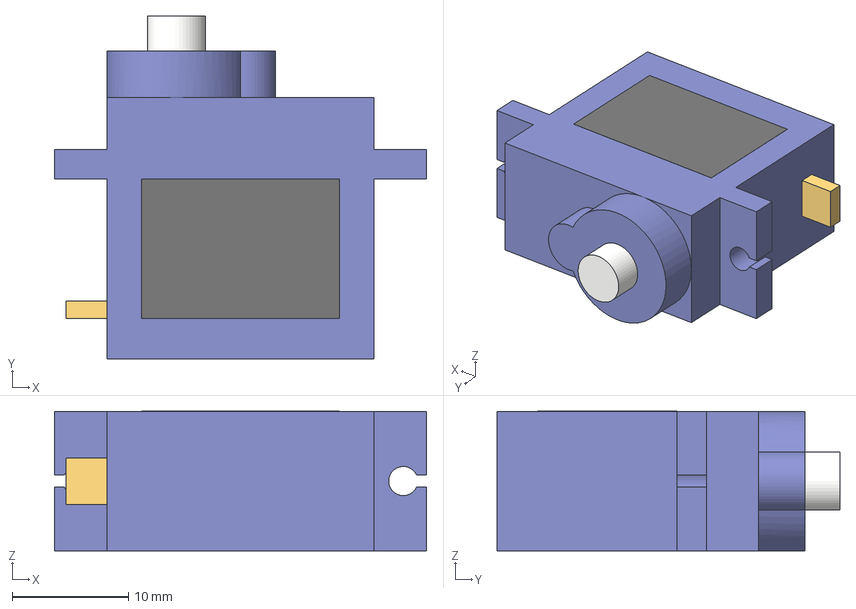
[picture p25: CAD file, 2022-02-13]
FiringMechAssembly/3D Designs/Final Design/Micro Servo 9g v2.step
32.0 x 29.5 x 12.0 mm

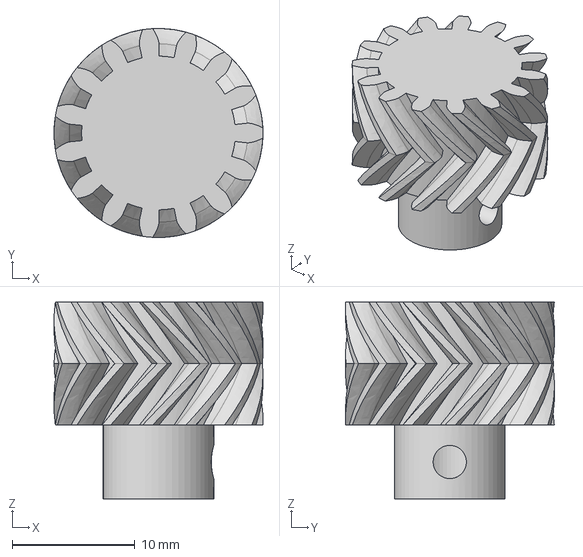
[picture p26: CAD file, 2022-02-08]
Pan-TiltAssembly/CAD_Files/Tilt_Pinion_15T.step
17.0 x 17.0 x 16.0 mm

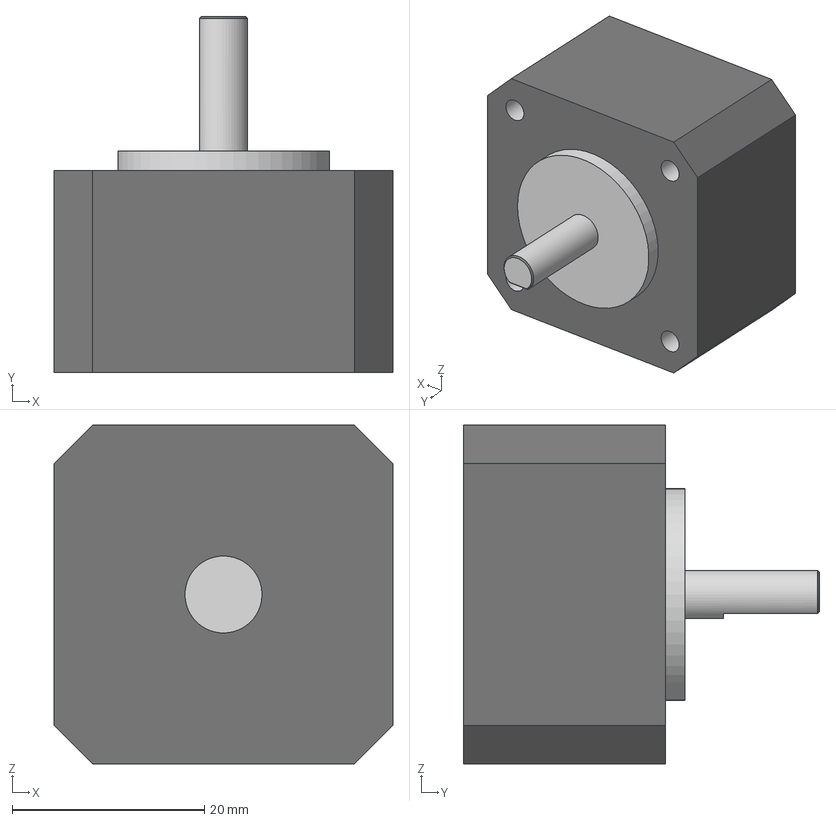
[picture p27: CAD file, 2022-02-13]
FiringMechAssembly/3D Designs/Final Design/35x35x20Stepper v1 v1.step
35.2 x 37.0 x 35.2 mm

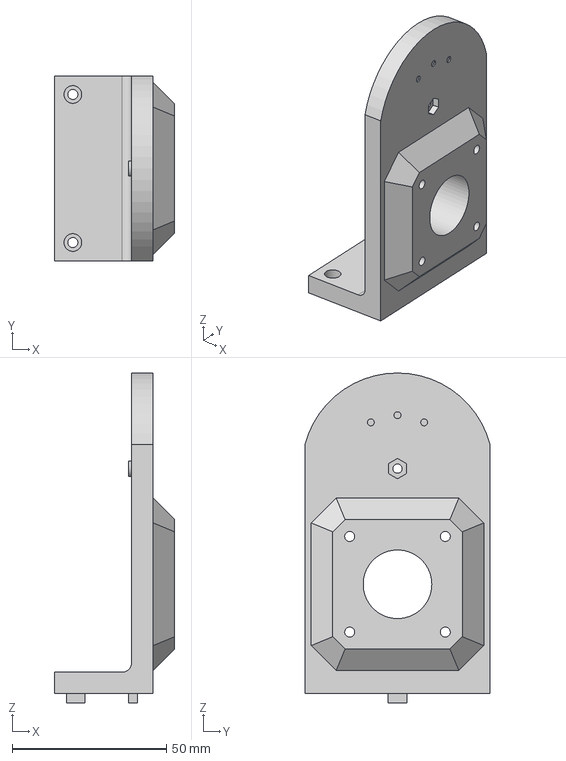
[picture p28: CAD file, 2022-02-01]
Pan-TiltAssembly/CAD_Files/Tilt_Gear_Stepper_Support.step
39.0 x 60.0 x 107.0 mm

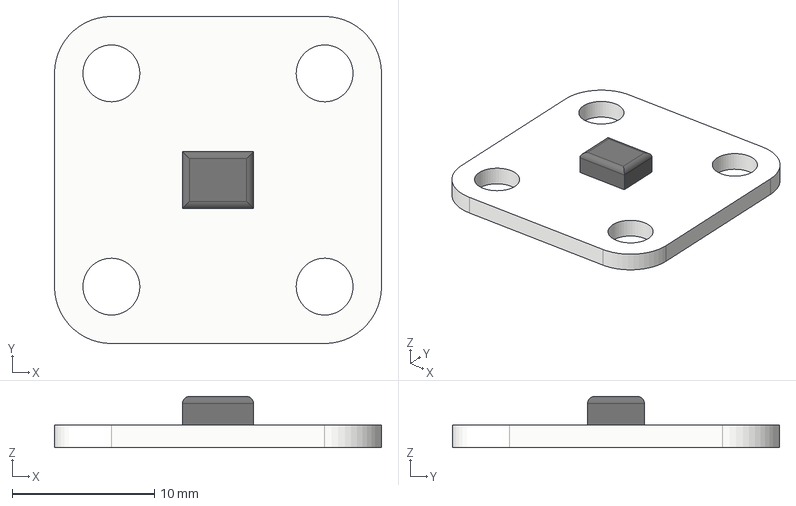
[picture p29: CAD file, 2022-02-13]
FiringMechAssembly/3D Designs/Final Design/AS5600 Magnetic Encoder v4.step
23.0 x 23.0 x 3.60 mm

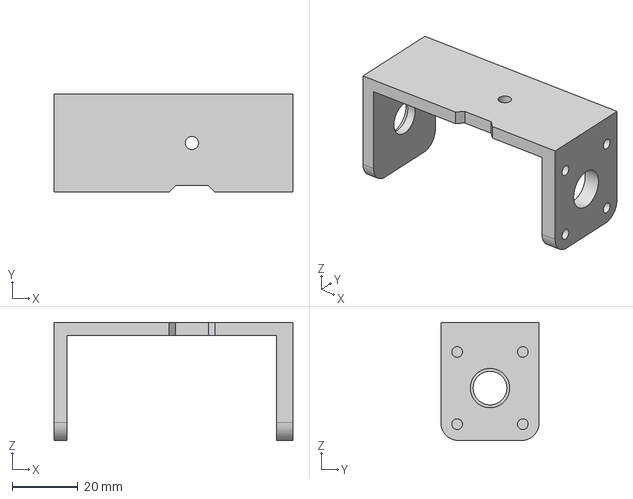
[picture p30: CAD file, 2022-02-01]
Pan-TiltAssembly/CAD_Files/Firing_Mech_Bracket_V1.step
72.8 x 30.0 x 36.0 mm

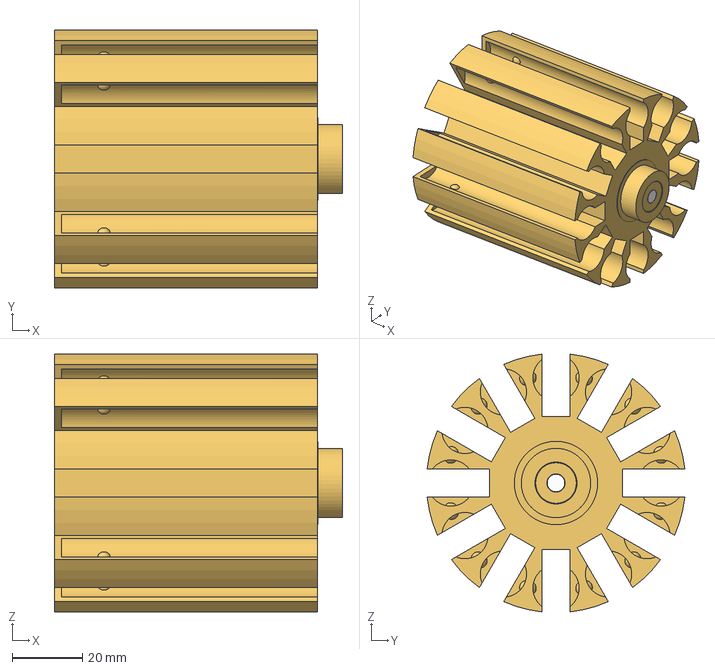
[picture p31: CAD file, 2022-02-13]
FiringMechAssembly/3D Designs/Final Design/12 Dart Magazine v13.step
82.2 x 73.6 x 73.6 mm

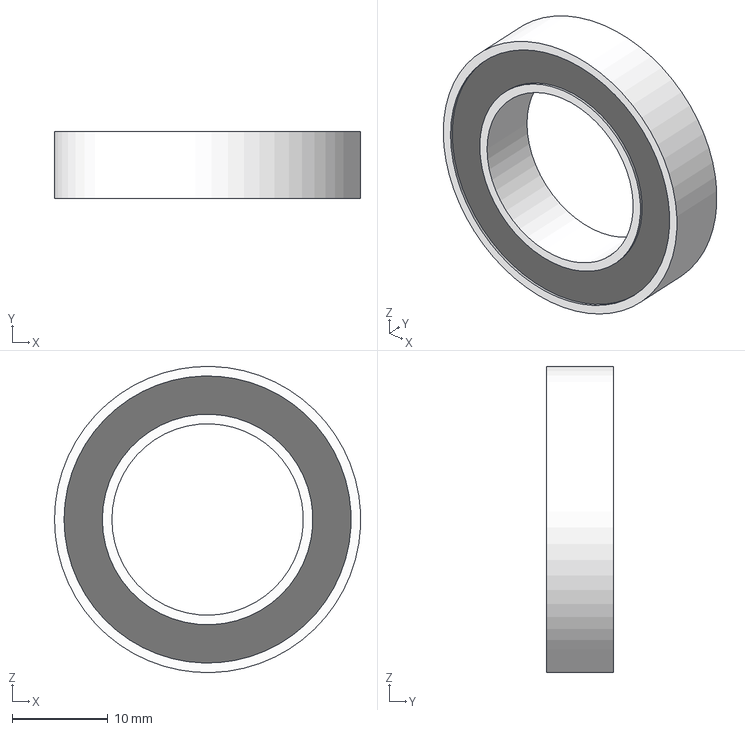
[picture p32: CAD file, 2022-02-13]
FiringMechAssembly/3D Designs/Final Design/20x32x7Bearing v1 v1.step
32.0 x 7.00 x 32.0 mm

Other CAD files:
FiringMechAssembly/3D Designs/Final Design/Servo Arm v8.step
FiringMechAssembly/3D Designs/Final Design/Nerf Bullet v3.step
FiringMechAssembly/3D Designs/Final Design/Launcher v5.step
FiringMechAssembly/3D Designs/Final Design/Stepper Holder v17.step
FiringMechAssembly/3D Designs/Final Design/Bearing Holder v17.step
FiringMechAssembly/3D Designs/Final Design/Firing Mech Design 1 v23.step

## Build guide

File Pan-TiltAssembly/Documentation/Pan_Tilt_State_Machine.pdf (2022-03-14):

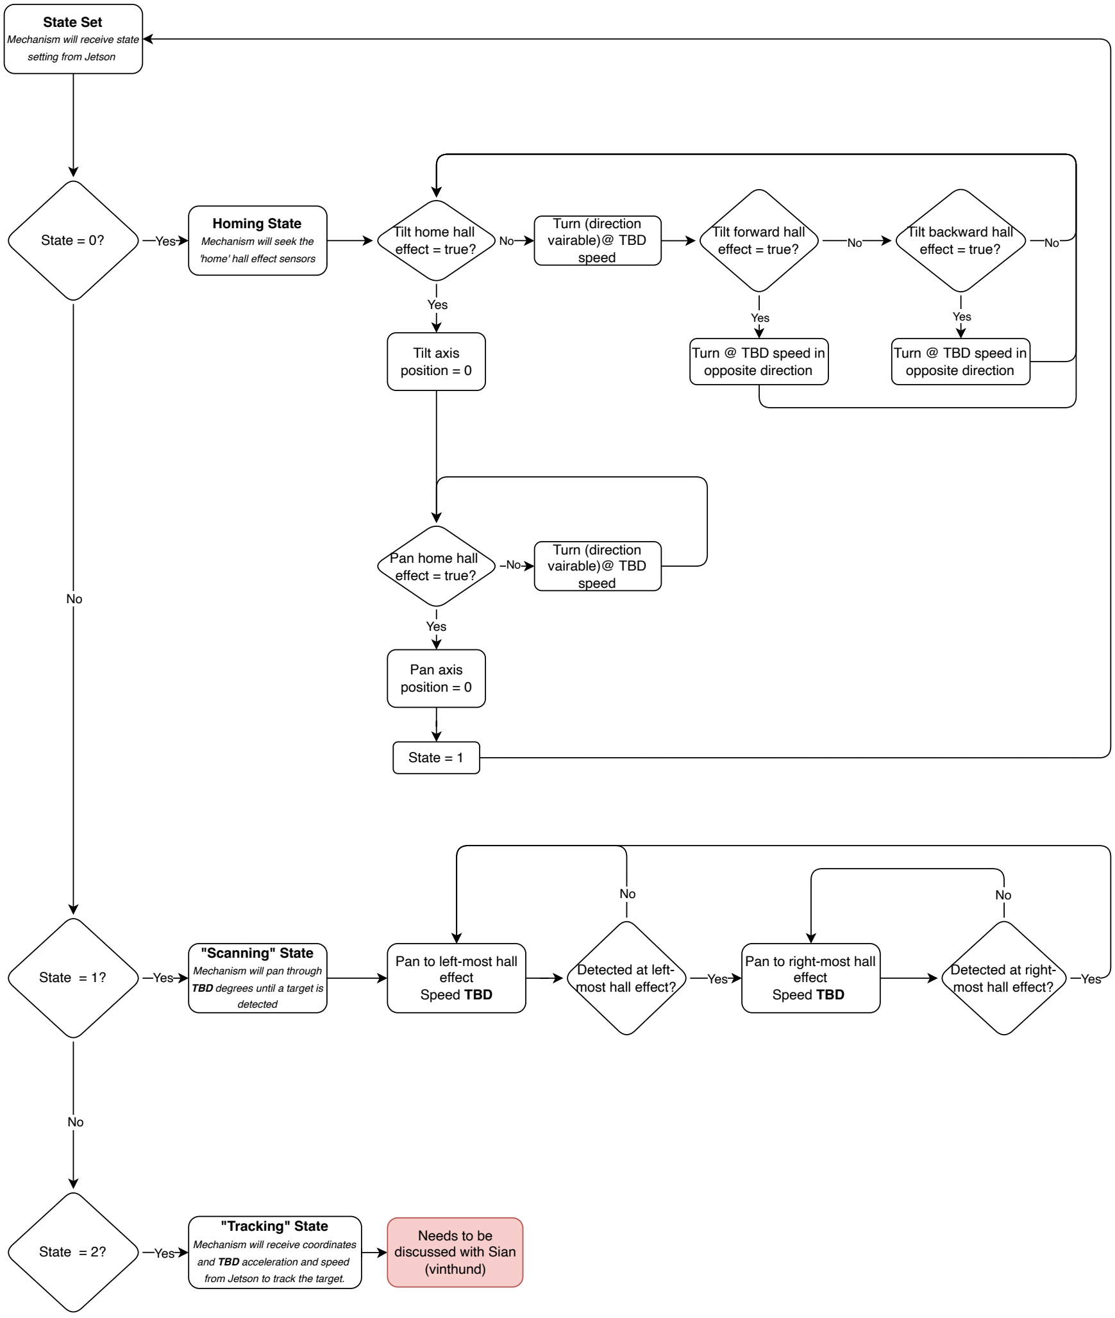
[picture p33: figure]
State Set; Mechanism will receive state; setting from Jetson; Yes; State = 0?; Homing State; Mechanism will seek the; 'home' hall effect sensors; State = 1?; "Scanning" State; Mechanism will pan through; TBD degrees until a target is; detected; State = 2?; "Tracking" State; Mechanism will receive coordinates; and TBD acceleration and speed; from Jetson to track the target.; Tilt home hall effect = true?; Turn (direction vairable)@ TBD speed; Tilt forward hall; effect = true?; Tilt backward hall effect = true?; Turn @ TBD speed in opposite direction; Pan home hall effect = true?; State = 1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

Pan by this distance

Tilt by this distance

The machine vision system will have to:

1. Identify the target
2. Identify "centre mass"
3. Calculate coordinates between target and centre of frame and send to pan/tilt mech
4. Decide if target is close enough to target to fire or not
5. Repeat 1-4 for each frame

The machine vision system should always seek to get the target back within the centre of frame.

It should do this by calculating how many steps the pan/tilt mechanism would need to traverse in both Pan/Tilt (X/Y) to get the target in the centre of frame.

If the machine vision system is capable of operating at the full frame-rate of the selected camera, these coordinates would update every 33.33ms.

The AccelStepper library being used to drive the stepper motors on the pan/tilt mech has lots of useful functions, but the pan/tilt mech process for receiving the coordinates from Jetson and then driving the mech to them needs to be done in tandem with Sian and Harshitha.
(https://www.airspayce.com/mikem/arduino/AccelStepper/classAccelStepper.html)

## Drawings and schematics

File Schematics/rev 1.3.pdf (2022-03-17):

## Power and Filtering

## Magazine Stepper Motor Control

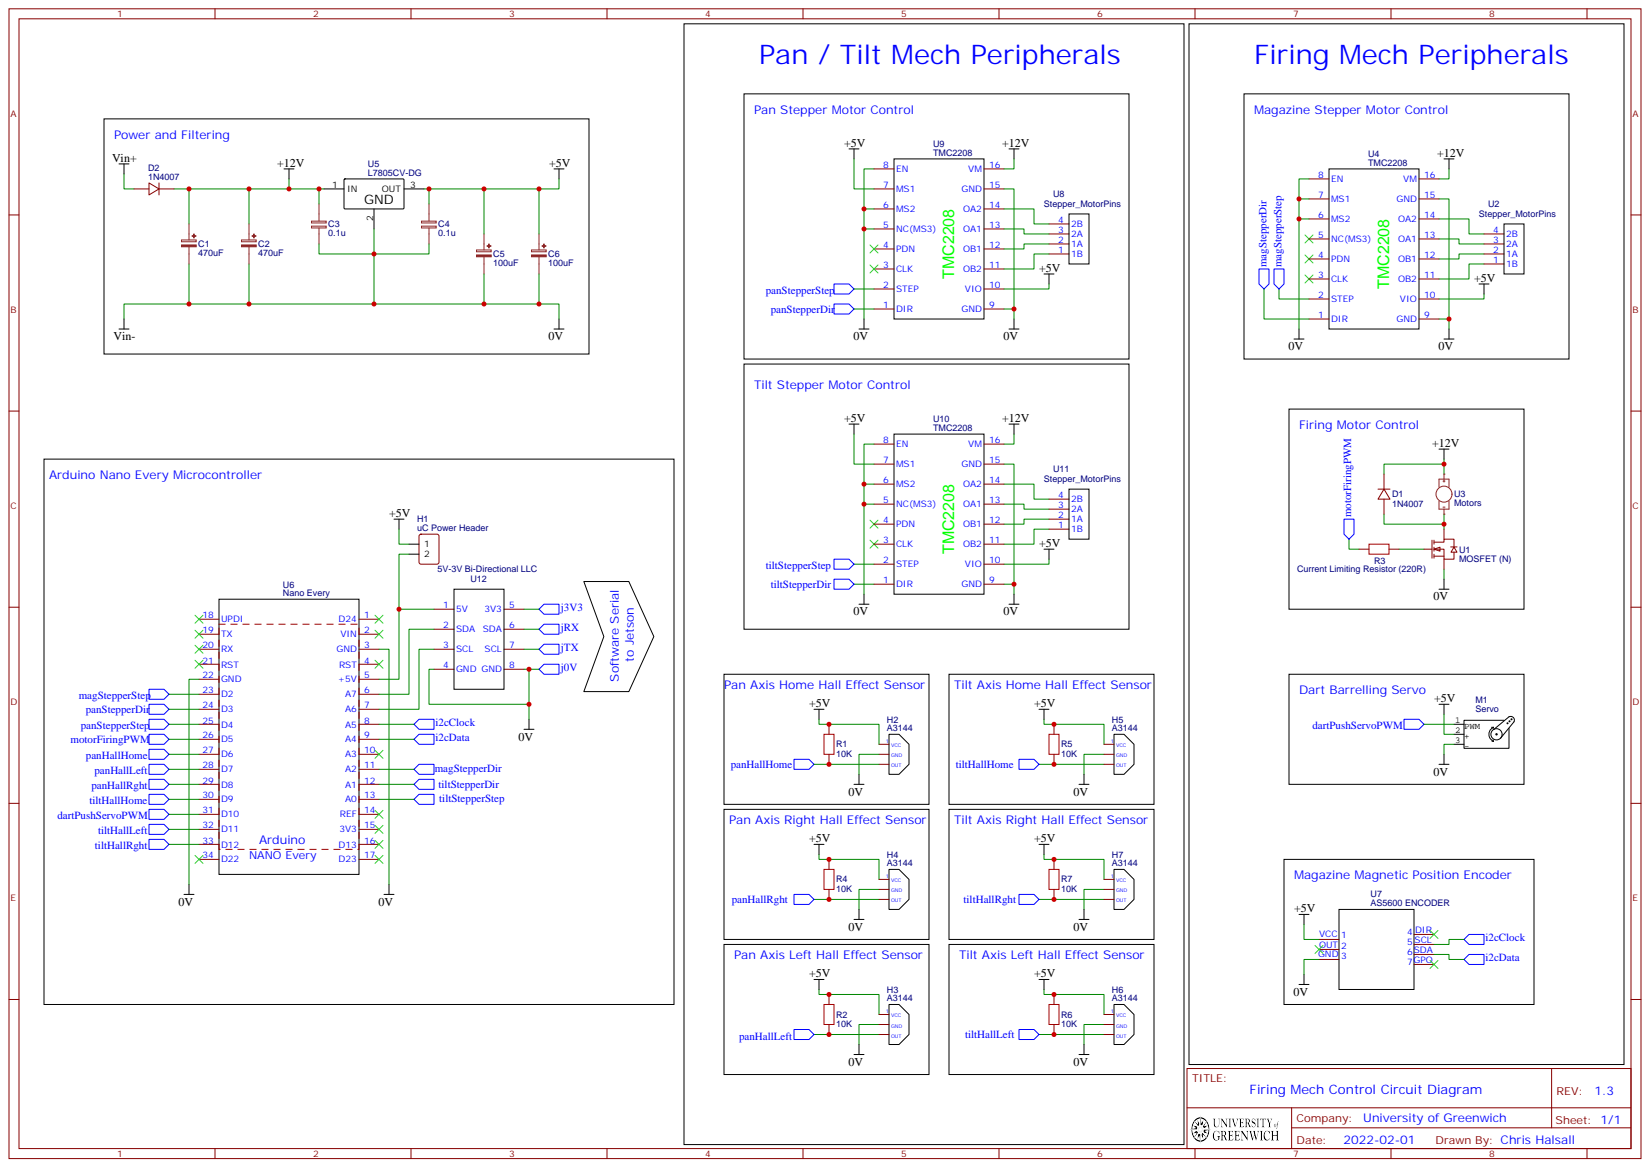
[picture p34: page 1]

Pan Stepper Motor Control

Tilt Stepper Motor Control

Arduino Nano Every Microcontroller

Pan Axis Home Hall Effect Sensor

Tilt Axis Home Hall Effect Sensor

Pan Axis Right Hall Effect Sensor

Tilt Axis Right Hall Effect Sensor

Magazine Magnetic Position Encoder

Pan Axis Left Hall Effect Sensor

Tilt Axis Left Hall Effect Sensor

Company: University of Greenwich

Drawn By: Chris Halsall

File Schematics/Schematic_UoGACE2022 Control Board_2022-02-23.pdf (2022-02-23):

## Power and Filtering Magazine Stepper Motor Control

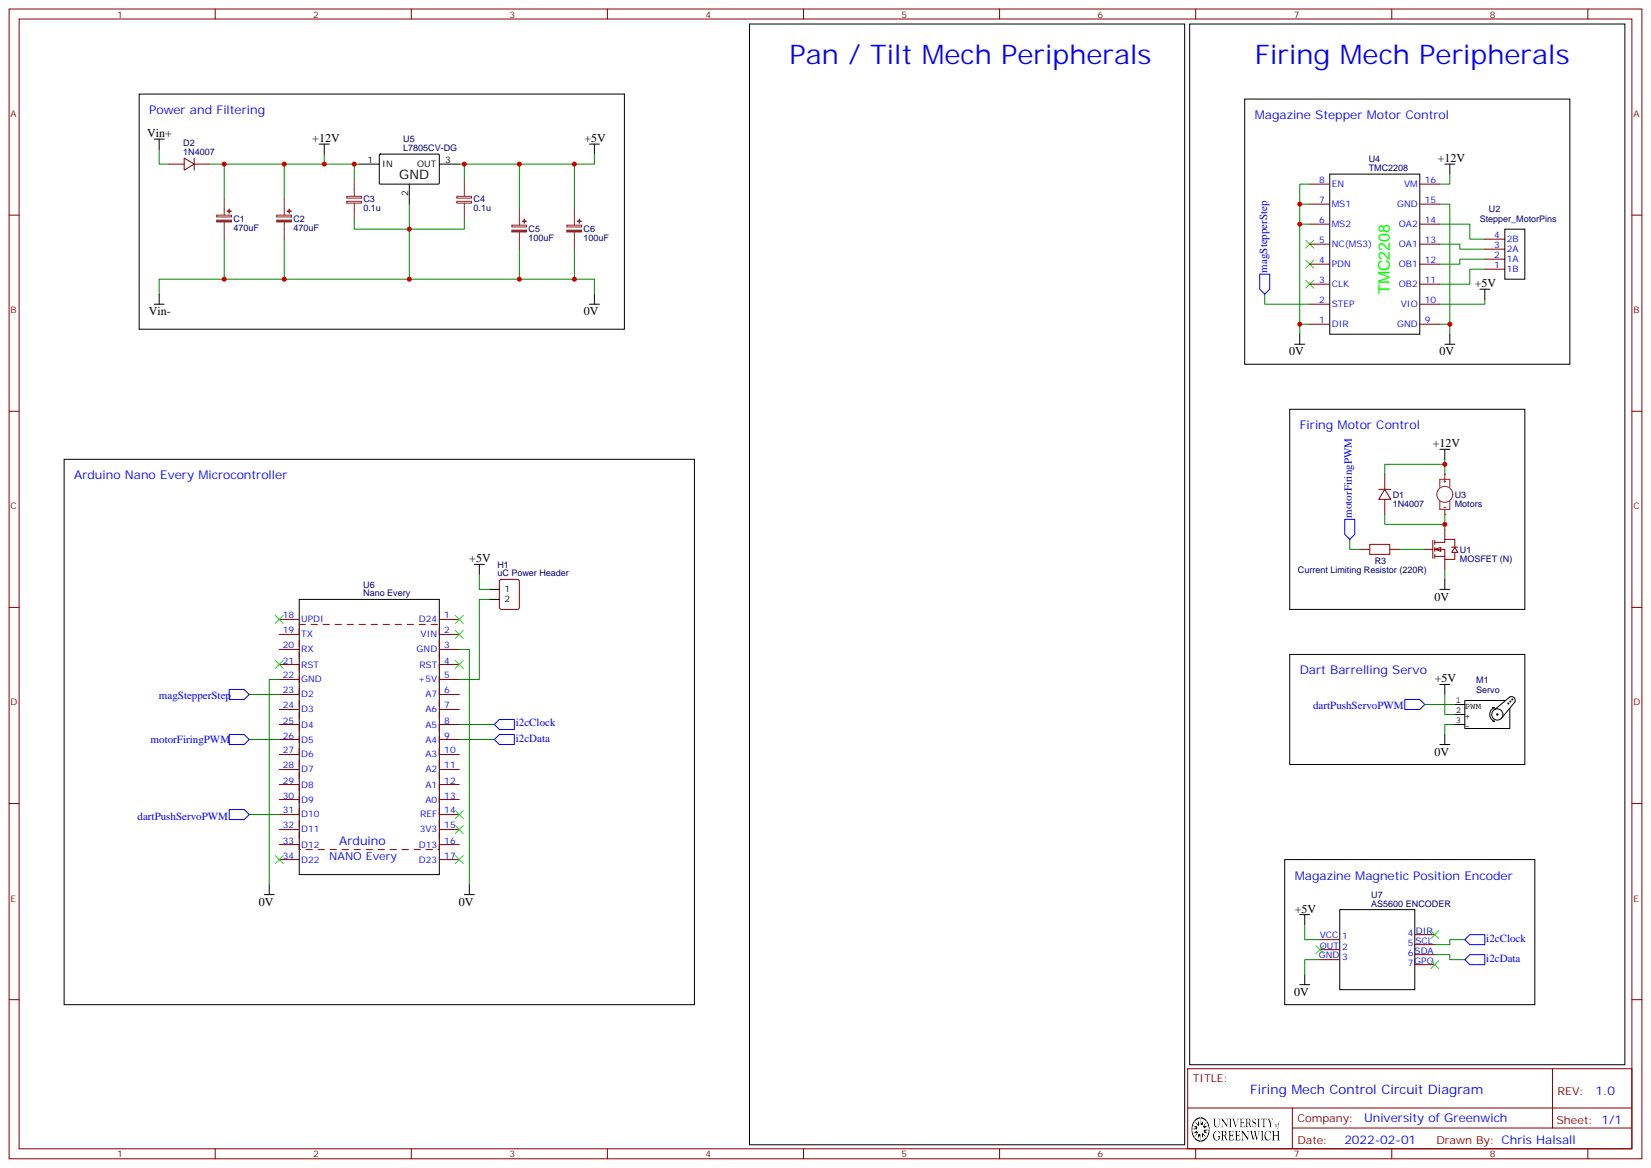
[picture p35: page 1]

Arduino Nano Every Microcontroller

Magazine Magnetic Position Encoder

Company: University of Greenwich

Drawn By: Chris Halsall

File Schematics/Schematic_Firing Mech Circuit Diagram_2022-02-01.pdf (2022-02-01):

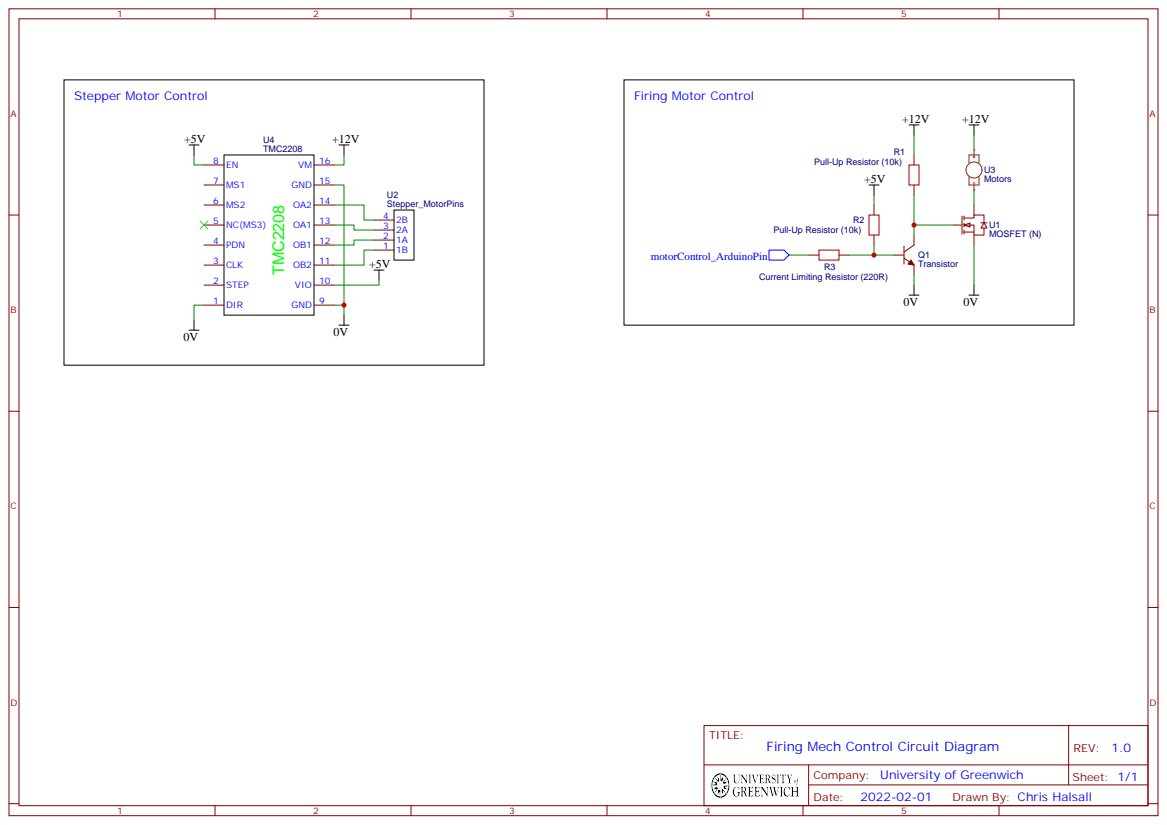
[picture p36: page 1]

Company: University of Greenwich

Drawn By: Chris Halsall

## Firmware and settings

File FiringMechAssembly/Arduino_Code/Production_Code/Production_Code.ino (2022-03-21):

#include <SoftwareSerial.h> // Standard Arduino library for bit banging serial data comms
#include <Servo.h>          // Standard Arduino library for controlling servos
#include <Ramp.h>           // Standard Arduino library used to interpolate between values
#include <Wire.h>           // Standard Arduino I2C library
#include <AS5600.h>         // AS5600 library can be found here: https://github.com/Seeed-Studio/Seeed_Arduino_AS5600 
#include <AccelStepper.h>   // AccelStepper library can be found here: https://github.com/waspinator/AccelStepper
                            // AccelStepper's class references can be found herehttps://www.airspayce.com/mikem/arduino/AccelStepper/classAccelStepper.html#details 

//Definitions
#define motorInterfaceType 1 // As stepper drivers are being used, this will configure AccelStepper to just send step pulses on a single output pin
#define vmaxPWM 30

//Stepper pins
const int ci_magStepPin = 2; // Defines the step pulse output pin
const int ci_magDirPin = A2; // Defines the direction output pin, low = move CCW, high = move CW

const int ci_panStepPin = 4;
const int ci_panDirPin = 3;
const int ci_tiltStepPin = A0;
const int ci_tiltDirPin = A1;

//Servo Pins - For firing mech
const int ci_servoPin = 10;

//Motor Pins - For firing mech
const int ci_motorPin = 5;

//Hall effect pins
const int ci_panHomeHallPin = 6;
//const int ci_panLeftHallPin = 7; // Not used
//const int ci_panRghtHallPin = 8; // Not used
const int ci_tiltHomeHallPin = 11; 
const int ci_tiltDownHallPin = 9;
const int ci_tiltUpHallPin = 8;

//Declarations
SoftwareSerial jSerial(A6, A7);   // Rx, Tx, Serial to Jetson
Servo magServo;                   // For firing arm servo on firing mech
ramp motorRamp;                   // For dart flywheels on firing mech
AMS_5600 magSensor;               // For magazines magnetic encoder
AccelStepper panStepper (motorInterfaceType, ci_panStepPin, ci_panDirPin);    // Pan axis on Pan/Tilt Assembly
AccelStepper tiltStepper (motorInterfaceType, ci_tiltStepPin, ci_tiltDirPin); // Tilt axis on Pan/Tilt Assembly
AccelStepper magStepper (motorInterfaceType, ci_magStepPin, ci_magDirPin);    // Stepper used to rotate magazine on firing mech

//Constants
const int ci_dartPos[12] = { 250 , 568, 938, 1275, 1609, 1973, 2293, 2616, 2949, 3332, 3668, 3991 };
const byte cb_servoIn = 140;
const byte cb_servoOut = 0;
const byte cb_vMaxPWM = 30;
const int ci_motorSpinUpPeriod = 5000;
const int ci_maxMagSpeed = 100;

//Variables
bool b_serialDebugPrint = false; // Enables serial debug text - Variable not currently used
bool b_panAxisHomed = false;     // Flag to confirm pan axis has been homed - Variable not currently used
bool b_tiltAxisHomed = false;    // Flag to confirm tilt axis has been homed - Variable not currently used
int i_stateMachine = 0;          // Store variable for state machine switch case - Variable not currently used
int i_tiltHomingDirection;       // 0 = was previously pointing up, 1 = was previously pointing down - Variable not currently used
byte b_darts = 0;                // Stores the number of darts shot

int i_panTargetCoord = 0;  // Store the target coordinate for the pan axis - Variable not currently used
int i_tiltTargetCoord = 0; // Store the target coordinate for the tilt axis - Variable not currently used

int i_panHomeHallDetect;   // Stores coordinate for where panHomeHallPin was detected
int i_tiltHomeHallDetect;  // Stores coordinate for calculated location of tiltHomeHallPin
int i_tiltDownHallDetect;  // Stores coordinate for where tiltDownHallPin was detected
int i_tiltUpHallDetect;    // Stores coordiante for where tiltUpHallPin was detected

int i_panScanRange = 200;  // Used in 'scanning_func' to define range of motion for pan axis
int i_tiltScanRange = 100; // Used in 'scanning_func' to define range of motion for tilt axis
bool b_panScanDir = 0;     // Used in 'scanning_func' to keep track of whether pan axis has finished panning in one direction
bool b_tiltScanDir = 0;    // Used in 'scanning_func' to keep track of whether tilt axis has finished tilting in one direction

String s_received = "";    // Stores the string received over USB serial
int i_x = 0;               // Stores the x co-ordinate received over USB Serial
int i_y = 0;               // Stores the y co-ordinate received over USB Serial
int i_n = 0;               // Stores the number of darts to fire received over USB Serial

void setup() 
{
  //Comms Setup
  Serial.begin(74880);
  Serial.println(">>>>>>>>>>>>>>>>>>>>>>>>>>>>>>>");
  Serial.println("Machine Vision Foam Dart Sentry");
  Serial.println(">>>>>>>>>>>>>>>>>>>>>>>>>>>>>>>");
  Wire.begin();

  //Firing Motor Setup
  digitalWrite(ci_motorPin, 0);

  //Servo Pin Setup
  magServo.attach(ci_servoPin);
  magServo.write(cb_servoOut);

  //Stepper Setups
  magStepper.setMaxSpeed(ci_maxMagSpeed);

  //Output pins
  pinMode(ci_panStepPin, OUTPUT);
  pinMode(ci_panDirPin, OUTPUT);
  pinMode(ci_tiltStepPin, OUTPUT);
  pinMode(ci_tiltDirPin, OUTPUT);
  pinMode(ci_magStepPin, OUTPUT);
  pinMode(ci_magDirPin, OUTPUT);
  pinMode(ci_motorPin, OUTPUT);

  //Input pins
  pinMode(ci_panHomeHallPin, INPUT);
  pinMode(ci_tiltHomeHallPin, INPUT);
  pinMode(ci_tiltDownHallPin, INPUT);
  pinMode(ci_tiltUpHallPin, INPUT);

  //Stepper Acceleration Settings
  panStepper.setMaxSpeed(1000.0);    //This sets the maximum speed, datatype is float.
  panStepper.setAcceleration(25.0);  //This sets the acceleration and deceleration rates in steps/s, datatype is float.
  tiltStepper.setMaxSpeed(1000.0);   //This sets the maximum speed, datatype is float.
  tiltStepper.setAcceleration(25.0); //This sets the acceleration and deceleration rates in steps/s, datatype is float.

  homing_func(); // Homes the mechanism before entering the main program loop
  home_mag(); // Homes the magazine lining up the first dart
}

//Loop Function
void loop() 
{
  /* Simple Loop Function to Demonstrate all functions of the pan/tilt and firing mechs.
   * After all homing, mech enters scanning function (else statement).
   * Instructions to fire can be sent to the mech via USB serial in the form "X Y N",
   * where X -> X co-ordinate, Y -> Y co-ordinate, N -> Number of darts to fire.
   * If a co-ordinate is give outside of its normal scanning range movement will be limited to within that range.
   * Once complete the mech will re-enter the scanning function.
   * The b_darts variable tracks the number of darts fired and prevents firing if all darts are expelled.
   */
  if(Serial.available()){
    s_received = Serial.readStringUntil('\n');
    sscanf(s_received.c_str(), "%d %d %d", &i_x, &i_y, &i_n); //Arrange received string into X, Y, and N ints
    
    //Clip X and Y co-ordinates to within the normal scanning range
    if(i_x > i_panScanRange) {
      i_x = i_panScanRange;
    }
    if(i_x < -i_panScanRange) {
      i_x = -i_panScanRange;
    }
    if(i_y > i_tiltScanRange) {
      i_y = i_tiltScanRange;
    }
    if(i_y < -i_tiltScanRange) {
      i_y = -i_tiltScanRange;
    }
    
    char message[50];
    snprintf(message, 50, "Targetting X: %d Y: %d -> %d darts", i_x, i_y, i_n);
    Serial.println(message);

    //Move Steppers to X and Y 
    panStepper.moveTo(i_panHomeHallDetect + i_x);
    tiltStepper.moveTo(i_tiltHomeHallDetect - i_y);
    while(panStepper.distanceToGo() + tiltStepper.distanceToGo() != 0) {
      panStepper.run();
      tiltStepper.run();
    }

    //Fire i_n number of darts
    spinUp();
    while(i_n != 0){
      if(b_darts < 12){
        goToDart(b_darts);
        fire();
        i_n--;
        b_darts++;
      }
      else{ //Catch if out of darts
        Serial.println("Run out of darts!!!");
        break;
      }
    }
    spinDown();
  }
  else { //Revert to scanning when no further commands remain
    scanning_func();
  }
}


//---------------- Custom Functions ----------------\\

void home_mag() //Contains the function for homing the magazine to dart zero
{
  goToDart(0);
}

void goToDart(byte dart) //Contains the function for selecting a dart
{
  while(1)
  {
    delay(30);
    int i_tmp = magSensor.getRawAngle();
    int i_d = ci_dartPos[dart] - i_tmp;
    if ( i_tmp > (ci_dartPos[dart] - 3) && i_tmp < (ci_dartPos[dart] + 3)) 
    {
      return 0;
    }
    else if ( i_tmp > ci_dartPos[dart]) 
    {
      magStepper.setSpeed(50); 
      magStepper.runSpeed();
    }
    else 
    {
      magStepper.setSpeed(-50); 
      magStepper.runSpeed();
    }
  }
}

void spinUp() //Contains the function for spinning up the firing motors
{
  motorRamp.go(0);
  motorRamp.go(cb_vMaxPWM, ci_motorSpinUpPeriod);
  while(motorRamp.update() != cb_vMaxPWM)
  {
    analogWrite(ci_motorPin, motorRamp.update());
  }
}

void spinDown() //Contains the function for spinning down the firing motors
{
  analogWrite(ci_motorPin, 0);
}

void fire() //Contains the function to fire the selected dart
{
  magServo.write(cb_servoIn);
  delay(500);
  magServo.write(cb_servoOut);
  delay(500);
}

void homing_func() //Contains the function for homing the pan/tilt head
{
  /*
    -- Homing Function --
    The code in this funciton will drive the pan/tilt head to its 'home' hall effect sensors.
    
    - Homing the tilt axis -
    (1) The tilt axis will first be poiting down as this is more secure for transit
    (2) Drive tilt axis up at a constant speed until the 'tiltUpHallPin' is detected 'low', then record current coordinate
    (3) Drive tilt axis down at constant speed until the 'tiltDownHallPin' is detected 'low', then record current coordinates
    (4) Calculate the midpoint between the coordinates for (2) and (3)
    (5) Drive tilt axis to calculated midpoint and stop tilt axis

    - Homing the pan axis -
    (1) Drive the pan axis around at a constant speed until 'panHomehallPin' is detected 'low' 
    (2) When 'panHomeHallPin' is detected 'low', stop the pan axis and record current coordinate

  */

  //Tilt Up till Limit 
  tiltStepper.setSpeed(-100);
  while(digitalRead(ci_tiltUpHallPin) == 1) // Hall effect output is low when magnet is detected
  {
    tiltStepper.runSpeed();
  }
  tiltStepper.stop();
  i_tiltUpHallDetect = tiltStepper.currentPosition();
  delay(200);

  //Tilt Down till Limit
  tiltStepper.setSpeed(100);
  while(digitalRead(ci_tiltDownHallPin) == 1)
  {
    tiltStepper.runSpeed();
  }
  tiltStepper.stop();
  i_tiltDownHallDetect = tiltStepper.currentPosition(); 
  delay(200);

  //Calculate mid then move to.
  if (i_tiltDownHallDetect > i_tiltUpHallDetect) 
  {
    i_tiltHomeHallDetect = ((i_tiltDownHallDetect - i_tiltUpHallDetect) / 2) + i_tiltUpHallDetect;
  }
  else 
  {
    i_tiltHomeHallDetect = ((i_tiltUpHallDetect - i_tiltDownHallDetect) / 2) + i_tiltDownHallDetect;
  }
  tiltStepper.moveTo(i_tiltHomeHallDetect);
  while(tiltStepper.currentPosition() != i_tiltHomeHallDetect)
  {
    tiltStepper.run();
  }
  tiltStepper.stop();
  // Possibly add 'i_tiltHomeHallDetect = tiltStepper.currentPosition(0);' here?
  // Parsing '0' into 'currentPosition' will set the current location as the Zero point for further coordinates which could be useful as.
  // Though this is possibly more relevant for simplifying 'tracking_func' logic, current implementation does work.
  delay(200);

  //Home Pan
  panStepper.setSpeed(100);
  while(digitalRead(ci_panHomeHallPin) == 1)
  {
    panStepper.runSpeed();
  }
  panStepper.stop();
  i_panHomeHallDetect = panStepper.currentPosition(); // If we parse '0' into currentPosition, the current location will be set as coordinate 0
  delay(200);
  
}// end of homing_func

void scanning_func() //Contains the function for 'scanning' for potential tartets
{
  /*
    -- Scanning Function --
    The code in this function drives pan and tilt axes between coordinates either side of their home positions.
    This will allow for the machine vision system to get a better view of potential targets infront of the system.

  */

  //Pan Stepper Control
  if(b_panScanDir == 0)
  {
    panStepper.moveTo(i_panHomeHallDetect - i_panScanRange);
  }
  else
  {
    panStepper.moveTo(i_panHomeHallDetect + i_panScanRange);
  }

  if(panStepper.distanceToGo() == 0) // 'distanceToGo' returns how many steps are left until the target value is met
  {
    b_panScanDir = !b_panScanDir;    // Setting this will cause axis to rotate in opposite direction
  }
    
  //Tilt Stepper Control
  if(b_tiltScanDir == 0)
  {
    tiltStepper.moveTo(i_tiltHomeHallDetect - i_tiltScanRange);
  }
  else
  {
    tiltStepper.moveTo(i_tiltHomeHallDetect + i_tiltScanRange);
  }

  if(tiltStepper.distanceToGo() == 0)
  {
    b_tiltScanDir = !b_tiltScanDir;
  }

  panStepper.run();
  tiltStepper.run();
}

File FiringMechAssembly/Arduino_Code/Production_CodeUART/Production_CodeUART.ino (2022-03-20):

/* UART Communications Code for Firing Mech
    Tested between Arduino and its Master, (Currently Raspberry Pi).
    Communication contents will consist of status codes to update the Raspberry Pi of its current status, and vice versa.
    This is an alternate version of its I2C Counterpart. This code was created due to the Arduino already using I2C to communicate with another device for the gun.
    Thus, another serial communication option had to be selected to make communication work.

    Rx <--> Tx
    Tx <--> Rx
    GND <--> GND

    Version 0.7.0
   Changes made:
    * Including SoftwareSerial Library to accept data over UART from Raspberry Pi.
    * Using "readStringUntil" to read information being sent from UART Serial.
    * Added requestEvent in main loop as it does not have a setup function anymore, unlike its I2C counterpart which did, thus not requiring for it to be called in void loop.
    * "Wire.write" replaced with mySerial.println due to using a decoder on Python's side. Just using write will not make it appear due to being in different character set.
    * New addition of firing code implemented onto base code.
    * Addition of byte variable ammo to check if there are bullets left before starting shooting.

*/
#include <SoftwareSerial.h>
#include <AccelStepper.h>
#include <Servo.h>
#include <Wire.h>
#include <AS5600.h>
#include <Ramp.h>

//Definitions
#define motorInterfaceType 1

//Stepper pins
const int ci_magStepPin = 2;
const int ci_magDirPin = A2;

//Servo Pins
const int ci_servoPin = 10;

//Motor Pins
const int ci_motorPin = 5;

//Declare objects of AccelStepper to handle pan and tilt axes, and magazine rotation
AccelStepper magStepper (motorInterfaceType, ci_magStepPin, ci_magDirPin);

//Declare Servo objects
Servo magServo;

//Declare RAMP objects
ramp motorRamp;

//Declare AS5600 Magentic Position Sensor
AMS_5600 magSensor;

//Const Variables
const int ci_dartPos[12] = { 250 , 568, 938, 1275, 1609, 1973, 2293, 2616, 2949, 3332, 3668, 3991 };
const byte cb_servoIn = 130;
const byte cb_servoOut = 10;
const byte cb_vMaxPWM = 30;
const int ci_motorSpinUpPeriod = 5000;
const int ci_maxMagSpeed = 100;

//String Variables
String received_str = "";

//Integer Variables
int toSend, x, y;

//Byte Variables
byte ammo = 0;

//Boolean Values
bool flag, trigger, movement = false;

//SoftwareSerial definition
SoftwareSerial mySerial(3, 4); // RX, TX

void setup()
{
  Serial.begin(115200);
  Serial.println(">>>>>>>>>>>>>>>>>>>");
  Wire.begin();
  while (!Serial) {
    ; // wait for serial port to connect. Needed for Native USB only
  }
  mySerial.begin(9600);
  //Firing Motor Setup
  digitalWrite(ci_motorPin, 0);

  //Output pins
  pinMode(ci_magStepPin, OUTPUT);
  pinMode(ci_magDirPin, OUTPUT);
  pinMode(ci_motorPin, OUTPUT);

  //Servo Pin Setup
  magServo.attach(ci_servoPin);
  magServo.write(cb_servoOut);

  //Stepper Setups
  magStepper.setMaxSpeed(ci_maxMagSpeed);

  /*
    //Example Sketch
    //Homes magazine, spins up motors, fires each dart, spinds down motors.
    home_mag();
    spinUp();
    for ( byte d = 0; d < 12; d++ ) {
      goToDart(d);
      fire();
    }
    spinDown();*/
  toSend = 1;
  delay(3000);
  flag = true;
}

void activate() {
  /*home_mag();
  spinUp();
  if (ammo < 12) {
    for ( ammo = 0; ammo < 12; ammo++ ) {
      goToDart(d);
      fire();
    }
  }
  spinDown();*/
}


// Function that sends data to Master (Pi). Unlike receiveEvent, the Wire.available confirmation loop cannot be used as it stops data being sent.
void requestEvent() {
  mySerial.println(toSend);
}

// Function that deals with status codes to control Arduino
void statusCodes() {
  //Static keyword used to create variable for only one function. This, unlike other variables, keeps its value after function calls, allowing it to
  // be compared with newer versions of values to make comparisons with them. This is used in this code to avoid the servo moving over to the same position again
  // even though it is receiving the same coordinates.
  static int x_old = 0;
  static int y_old = 0;

  if (received_str == "1") {
    Serial.println("Raspberry Pi - Connection Established");
  } else if (received_str == "2") {
    Serial.println("Raspberry Pi - Data Received");
  } else if (received_str == "100") {
    Serial.println("Raspberry Pi - Status OK");
  } else if (received_str[0] == '(' ) {
    Serial.println("Coordinates Received, Ready to Delete Target!");
    //sscanf is used here to read formatted input from a string, then assigns the values to be read onto integer varianbles.
    // in this case, they are set to coordinate "x" and "y" variables.
    int r = sscanf(received_str.c_str(), "(%d, %d)", &x, &y);
    snprintf(out, 30, "X: %d, Y: %d", x, y);

    Serial.print("X: ");
    Serial.println(x);
    Serial.print("Y: ");
    Serial.println(y);

    /*Activates shooting after receiving coordinates. However, this is an unfinished part due to the
      code logically needing to move to its position before shooting.
    */
    activate();
    // Below conditional statement checks if the current coordinate variables are equal to its previous versions stored on the static int variables.
    // In the case it is, the movement flag is set to false, blocking movement from occuring as no change has occured.
    // However, in the case that it is not the same as its previous version, movement is set to true, then the coordinate variables are stored in the static int variables,
    // so as to be compared to the next values sent.
    if (x == x_old && y == y_old) {
      movement = false;
    } else {
      movement = true;
      x_old = x;
      y_old = y;
    }
  }
}

//The Below function works on blocking strings/characters from appearing except brackets and numbers.
void convertToInt() {
  int n = received_str.toInt();
  if (n > 0 || received_str[0] == '(') {
    //Serial.println(received_str);
    received_str = "";
  } else {
    received_str = "";
  }
}

void loop()
{
  delay(100);
  requestEvent();
  received_str = mySerial.readStringUntil('\n');
  toSend = 100;
  statusCodes();
  convertToInt();
} //End of 'loop'


void home_mag() //Contains the function for homing the magazine to dart zero
{
  goToDart(0);
}

void goToDart(byte dart) //Contains the function for selecting a dart
{
  while (1)
  {
    delay(30);
    int i_tmp = magSensor.getRawAngle();
    int i_d = ci_dartPos[dart] - i_tmp;
    if ( i_tmp > (ci_dartPos[dart] - 3) && i_tmp < (ci_dartPos[dart] + 3)) {
      return 0;
    }
    else if ( i_tmp > ci_dartPos[dart]) {
      magStepper.setSpeed(50);
      magStepper.runSpeed();
    }
    else {
      magStepper.setSpeed(-50);
      magStepper.runSpeed();
    }
  }
}

void spinUp() //Contains the function for spinning up the firing motors
{
  motorRamp.go(0);
  motorRamp.go(cb_vMaxPWM, ci_motorSpinUpPeriod);
  while (motorRamp.update() != cb_vMaxPWM)
  {
    analogWrite(ci_motorPin, motorRamp.update());
  }
}
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

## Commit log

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2022-01-25 Create AS5600 Magnetic Rotary Encoder Datasheet.pdf
    AS5600 Datasheet to be used as resource
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2022-01-25 [New] Firing Mech Bracket V1.
    [Firing_Mech_Bracket_V1.step]
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2022-02-01 [Mod] Rounded off corners and tolerance tweaks.
    [Firing_Mech_Bracket_V1.step]
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2022-02-01 <Update V1.1> Addition of Serial Communication code between Raspberry Pi and Arduino. Contents Include a simple Test Code in which Python Controls a Fan by sending messages to the Arduino
2022-02-01 [New] Firing mech support bracket.
    [Firing_Mech_Bracket_Support.step]
2022-02-01 Firing Mech Concept Design STEP files
    [Circular 20 Dart Magazine Concept v2.step, Firing Mech Concept 1 v6.step]
2022-02-01 [New] Tilt gear and stepper motor support.
    [Tilt_Gear_Stepper_Support.step]
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2022-02-01 [New] Tilt pinion with 15 teeth.
    [Tilt_Pinion_15T.step]
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2022-02-07 <Version 1.1.2> Update: Addition of connection acknowledgement between Arduino and Raspberry Pi through UART Serial Communication
2022-02-07 <Update: Version 1.3> More Bug Fixes, Successfully implemented communication establishment between Arduino and Raspberry Pi through UART. This new Version, 1.3, now features a quote unquote heartbeat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
2022-02-08 [New] Code for quickly testing the functionality of the stepper motors on the pan/tilt head.
2022-02-08 [Fix] Changed grub screw hole diameter from 3mm to 2.7mm to improve fitment.
2022-02-08 [Fix] Addition of an end stop to the pinion to improve alignment with the main tilt gear.
    [Tilt_Pinion_15T.step]
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2022-02-09 [Fix] Added 'run' function call at the end of the main loop.
    [DualStepperTest.ino]
2022-02-13 Final 3D designs for Firing Mech
    [12 Dart Magazine v13.step, 20x32x7Bearing v1 v1.step, 35x35x20Stepper v1 v1.step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]
2022-02-13 [New] Flow diagram that proposes a switch case state machine for the pan-tilt head - This commit contains the proposed 'homing' algorithm.
2022-02-14 [Fix] In testing it was found that the torque of the motor was enough to drive the grub screw out of the pinion and allow the steppers shaft to spin freely inside the pinion. A mating flat has been a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
2022-02-15 [Addition] Added foam sheet used to dampen the vibrations from the lazy susan bearing.
2022-02-19 [Mod] Adjusted the hall effect sensor mounting locations.
    [Firing_Mech_Bracket_Support.step]
2022-02-19 [New] A mount for the hall effect sensors on the pan axis.
    [Hall_Effect_Pan_Mount.step]
2022-02-19 [Addition] Rev 3 - Addition of Hall Effect Pan Mount and relevant fixings.
2022-02-23 Continued Firing Mech Code Testing
    Integrating testing with the development of the custom circuitboard.
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2022-02-24 [Fix] Adjusted fit of hall effect mount to better hold the sensor.
    [Hall_Effect_Pan_Mount.step]
2022-02-24 [Edit] Added prompts for where contibutors should be inserting their summary of work.
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2022-02-24 <Update> Changes made to communications code including moving all communications code to a seperate directory. Along with this, other changes such as the implementation of I2C has been added into thi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
2022-02-25 <Update V1> Implementation of other communication codes into main I2C Code. Deletion of other excess files not used in project.
2022-02-25 [Update] Version 1.1 of Python I2C Code, deletion of other experimental files
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2022-02-25 [Update] Version 1.2 of Arduino Code. Any character sent from Pi to Arduino becomes jumbled up however, more to fix.
    [ArduinoSlaveI2C.ino]
2022-02-25 [Update] Version 1.2 of ArduinoComms code. More changes to be made, current code can output characters, but not correctly.
    [ArduinoSlaveI2C.ino]
2022-02-25 [Update] Version 1.2.1 Arduino Comms Code: Current Code cannot check if the received input is a string or a number. Condition loop within "void(loop)" does not work properly as of yet.
    [ArduinoSlaveI2C.ino]
2022-02-25 [Update] Version 1.2.2 of Arduino Comms Code. Changes include now setting received information from Pi to integer, rest of information will be contained in code.
2022-02-26 [UPDATE] Minor Changes made including: addition of function to send data to Pi, addition of potentiometer code to send data to Pi, fixing data not being sent to Pi through addition of "onRequest".
    [ArduinoSlaveI2C.ino]
2022-02-26 [UPDATE] Version 1.4.0 of Python Code. Minor changes implemented such as addition of i2cRead function, keyboard interrupt feature to stop program in case it starts acting strangely, removal of excess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
2022-02-27 [Fix] Changed fitment of hall effect sensor mounting points.
    [Firing_Mech_Bracket_Support.step]
2022-02-27 [New] Code template for testing control of the pan/tilt assembly based on inital state machine flowchart.
2022-03-01 <repair> conflicts with merges by @kamyar123
    [Circular 20 Dart Magazine Concept v2.step, Firing Mech Concept 1 v6.step, Firing_Mech_Bracket_V1.step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]
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2022-03-03 [UPDATE n DEPRECATION] Version 1.5.1 of RaspberryPi Master COde, modifications mande including addition of new function StatusCodes, removal of encoding variable and additional changes to allow for s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
2022-03-04 [UPDATE] Major changes made to i2cRead function, addition of new OS module, removal of redundant code to increase efficiency and manipulation of new OS module to clear terminal whenever certain thres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
2022-03-05 [UPDATE] Heartbeat signal added, requestEvent function fixed, connection established feature added, status codes function added.
    [ArduinoSlaveI2C.ino]
2022-03-05 [UPDATE] Version 1.6.1 of Arduino Code. Heartbeat signal added, requestEvent function fixed, connection established feature added, status codes function added.
    [ArduinoSlaveI2C.ino]
2022-03-05 [UPDATE] Version 1.6.0 of Arduino Code and Version 2.0.4 of Python Code: More Minor changes and bug fixes along with big implementations such as heartbeat signal. Arduino code changes include heartbe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
    [ArduinoSlaveI2C.ino]
2022-03-05 [UPDATE] Version 2.0.4 of Python Code. Temporary deletion of Arduino code due to odd clash. Changes of Python code include implementation of new error code, heartbeat signal and bug fix of status cod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
2022-03-05 [UPDATE] Version 1.6.1 of Arduino Code: Re-addition of Arduino Code due to merge clash error. Implementations include new connection established message and a heartbeat signal, along with fixes made 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
    [ArduinoSlaveI2C.ino]
2022-03-07 [Mod] Increased length of location pin such that it can be accessed more easily.
    [Hall_Effect_Pan_Mount.step]
2022-03-07 Firing Mech Development
    Continued testing of arduino firing mech code
    Addition of Parts List and component datasheets
    Movement of .step files to match pan/tilt folder structure.
    [12 Dart Magazine v13.step, 20x32x7Bearing v1 v1.step, 35x35x20Stepper v1 v1.step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]
2022-03-07 Updated Parts list for PSU Case
    [PSU Case v1.step]
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2022-03-08 [Merge] Bringing branch 'ad4646d' up-to-date with main.
    [12 Dart Magazine v13.step, 20x32x7Bearing v1 v1.step, 35x35x20Stepper v1 v1.step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]
2022-03-08 [BUG FIXES] Addition of a new exception which deals with the RemoteI/O Error whenever the connection between the Pi and the Arduino is severed
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2022-03-09 [UPDATE] Version 1.6.4 of Arduino Code featuring removal of SerialTestUSB, addition of new variables to Arduino and removal of H bridge codes
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2022-03-09 [New] Screenshot of CAD highlighting support bracket locator pins that help to ensure the support brackets are mounted square to eachother on the pan gear.
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2022-03-10 [UPDATE] Version 2.1.7 of Arduino Code, major changes including addition of servo functions, functions that capture coordinates and translate them to be used by servo's, removal of unused variables a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
2022-03-10 [UPDATE] Version 2.1.0 of Raspberry Pi Python Master Code. Changes made include increase of clearing range of command line to 200 counts along with the removal of heartbeat due to bugs.
2022-03-10 [UPDATE] Version 2.1.9 of Arduino Code. Changes include removal of startup function along with addition of static bytes, which can store older version of coordinates before changing.
2022-03-11 [UPDATE] Version 2.2.0 of Python Master Code. New feature includes addition of new function named 'setCoordinate' which receives coordinates from whatever is setting it, then sends it over I2C.
2022-03-11 [UPDATE] Version 2.3.0 of Arduino Code. New modifications feature removal of startup function and moving its contents to "void setup()", addition of static variables to store old versions of incoming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
    [ArduinoSlaveI2C.ino]
2022-03-11 Update README.md
    Addition of new image to show what I2C connections look like.
2022-03-11 [UPDATE] Version 2.3.1 of Arduino Code. New changes include ammo checking condition and shooting trigger. More details in comments.
2022-03-11 [UPDATE] Version 2.3.2 of Arduino Code. Changes made include ammo checker condition and simplifying servo definitions onto one line.
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2022-03-12 [RESTORATION] Restoring current version of Python due to version revert done on Github. Version 2.2.3 Python Master Code.
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2022-03-16 [Fixes and Additions] Fixed mistake of teammate made on Readme. Changes also include new additions of test codes for both I2C and Serial
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2022-03-16 [Revert] Reverting code back to commit: 'Further Development' (58091b7ea34deca24a9998f211210405cbfdaaad) by ch6941r.
    [Component_Testing.ino]
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2022-03-17 [UPDATE VERSION 0.6.1 PYTHON] - Added comments, Added a ValueError to capture disconnections from Arduino, Added feature logging oncoming messages along with correcting minor mistake of functions bei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
    [PythonMasterUART.py, UARTCommTest.ino]
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2022-03-17 [MINOR CHANGES] - Arduino Version 0.4.2. Minor changes include replacement of I2C comments with UART along with an explanation of code's nature such as the firing and pan tilt test.
    [UARTCommTest.ino]
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2022-03-21 Coding and Readme
    - Repaired circuitry photo link in README
    - Corrected some errors relating to pointers and data formatting
    [Production_Code.ino]
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
